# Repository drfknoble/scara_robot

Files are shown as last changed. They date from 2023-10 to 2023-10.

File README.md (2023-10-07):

# Selective Compliance Articulated Robot Arm (SCARA) Project








## Introduction

Welcome to my repository for my Selective Compliance Articulared Robot Arm (SCARA) project.

<!-- <div>
    <img src="./cad/renders/back.png" style="height:240px;">
    <img src="./doc/photos/back.jpg" style="height:240px;">
</div> -->

## Motivation

I started this project because commercial SCARA robots are very expensive and there any low-cost options for me to use in my teaching or research.

## Aims

The aims of this project included:
- Developing a low-cost, SCARA robot that can be used to teach students about mechatronics and robotics.

## Objectives

The objectives of this project included:
- Creating accessible Computer Aided Design (CAD) files.
- Creating accessible Electronics Design Automation (EDA) files.
- Creating accessible source code and software libraries.
- Creating an easy-to-assemble mobile robot that uses a microcontroller, stepper motors, and rotational sensors.

## Repository Structure

The repository is organised as follows:

```console
scara_project/         
    cad/                          
        fabrication/
        parts/
        sub_assemblies/   
    doc/                                   
    eda/
        manipulator_pcb/        
    src/
        esp32_program/
        my_bringup/
        my_scara_1_0_movit_config/
        my_scara_support/
```

All CAD files can be found in the `cad/` sub-directory. I used SolidWorks to create the 3D models of the robot's parts, sub-assemblies, and assembly. Files neeeded to fabricate the robot can be found in the `fabrication/` sub-directory.

All EDA files can be found in the `eda/` sub-directory. I used KiCAD to create the PCB for the robot. Files need to fabricate the PCB can be found in the `manipulator_pcb/` sub-directory.

All source code and software libaries are included in the `src/` sub-directory. I used an ESP32 as the robot's microcontroller and programmed it using PlatformIO's Arduino framework. The ESP32's source code can be found in the `esp32_program/` sub-directory. I also developed a ROS 2 package that makes use of ROS 2 Control and Moveit 2. The package's launch file can be found in the `my_bringup/` sub-directory. 

Documentation is included in the `doc/` sub-directory. I've included a Bill of Materaisl (BOM) file, which includes the compenents used.

## Tools Used

I used the following tools in this project:
- SOLIDWORKS.
- KiCAD.
- Microsoft Visual Studio Code and PlatforIO.
- ROS 2.

Get FreeCAD here: https://www.freecadweb.org/.  
Get KiCAD here: https://www.kicad.org/.  
Get Visual Studio Code here: https://code.visualstudio.com/.  
Get PlatforIO from here: https://platformio.org/. 

## Credit

Dr Frazer K. Noble  
http://drfknoble.com

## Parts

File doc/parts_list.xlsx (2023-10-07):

Item | Description | URL
1 | CNC kit | https://www.amazon.com/Professional-arduino-Mechanical-Endstop-DRV8825/dp/B06Y2BSCL7
2 | Encoder | https://www.amazon.com/Diitao-Magnetic-Precision-Induction-Measurement/dp/B0B4NNK14X
3 | 35 mm thrust bearings | https://www.amazon.com/uxcell-Single-Direction-Thrust-Bearings/dp/B07G847G75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
4 | 40 mm thrust bearings | https://www.amazon.com/uxcell-Single-Direction-Thrust-Bearings/dp/B07G829LM8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
5 | 8 mm Radial bearings | https://www.amazon.com/Bearings-Skateboard-Shielded-Miniature-Skateboards/dp/B07R7PR72H
6 | GT2 belt kit | https://www.amazon.com/3Dman-Timing-Closed-Rubber-Printer/dp/B07WP6VJ66
5 | Arduino Uno | https://mecha4makers.co.nz/product/arduino-uno-clone-usb-b/
5 | CNC shield | https://mecha4makers.co.nz/product/cir-cnc-sh-v3-o1/
15 | Motor driver | https://mecha4makers.co.nz/product/a4988-stepstick-style-stepper-driver-red/
15 | Stepper motor | https://mecha4makers.co.nz/product/17hs3401-s5f-20200829-stepper-motor-5mm-shaft-with-flat/
3 | Encoder | https://www.amazon.com/Alinan-Magnetic-Precision-Induction-Measurement/dp/B09QYC916Q
40 | 8 mm bearing | https://mecha4makers.co.nz/product/ball-bearing-plain-id-6mm/ | Note: | Please order "Plain – ID 8mm OD 22mm Width 7mm 608ZZ" type.
5 | GT2 belt | https://mecha4makers.co.nz/product/gt2-6mm-belts/ | Note: | Please order "Open belt, GT2 x 6mm, polyurethane (black), steel cord (per meter) "
20 | GT2 pulley | https://mecha4makers.co.nz/product/gt2-x-6mm-pulleys-5mm-bore/ | Note: | Pulley GT2 x 6mm wide, 20 teeth, 5mm bore

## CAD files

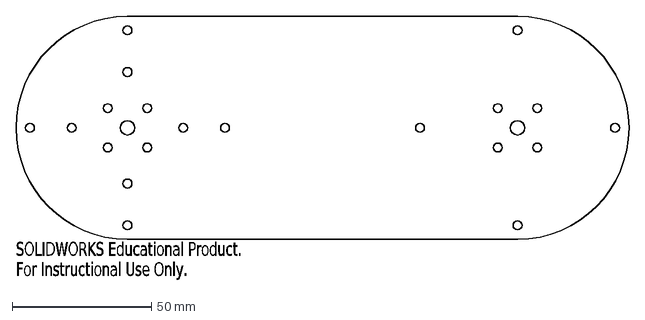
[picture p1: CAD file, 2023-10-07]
cad/fabrication/link_1_bottom.DXF
SOLIDWORKS Educational Product.
For Instructional Use Only.

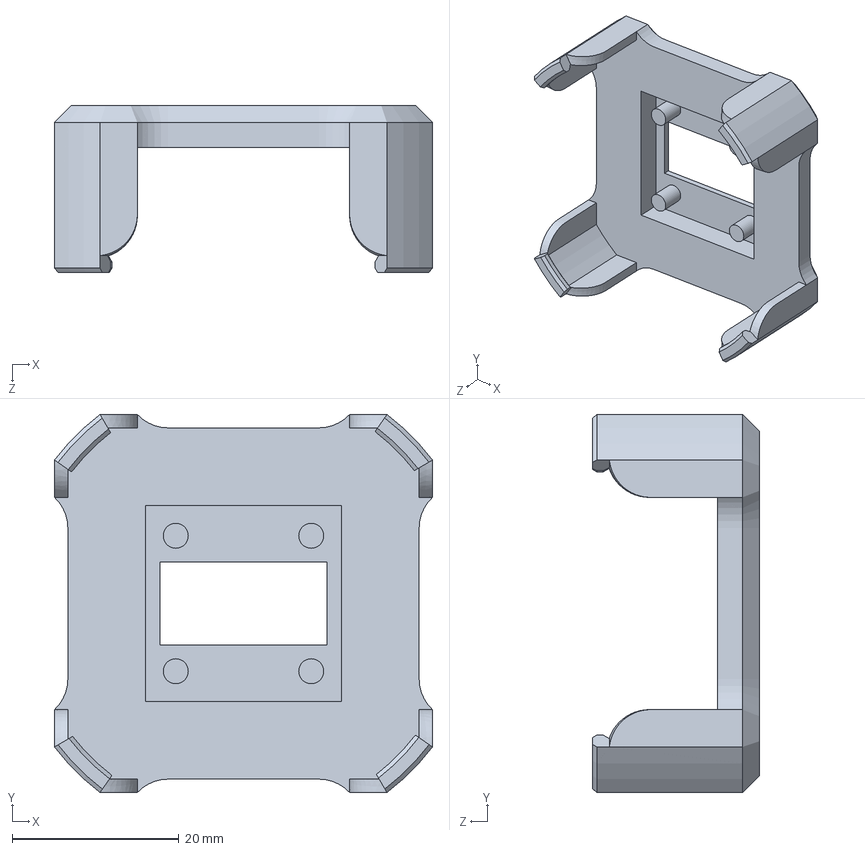
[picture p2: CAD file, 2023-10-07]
cad/parts/encoder_holder.SLDPRT
45.4 x 45.4 x 20.0 mm

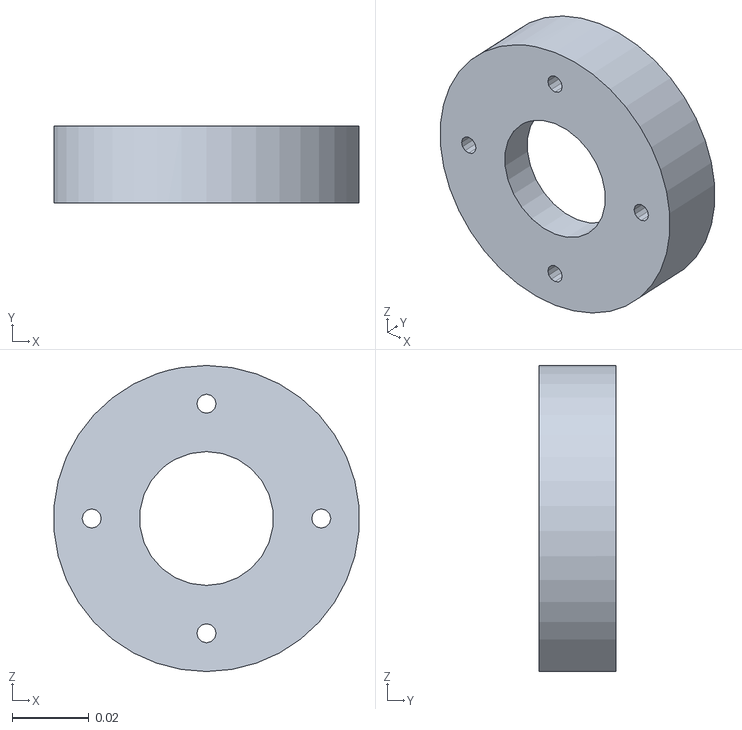
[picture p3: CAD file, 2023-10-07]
src/manipulator/meshes/coupler_1.STL
0.0797 x 0.02 x 0.08

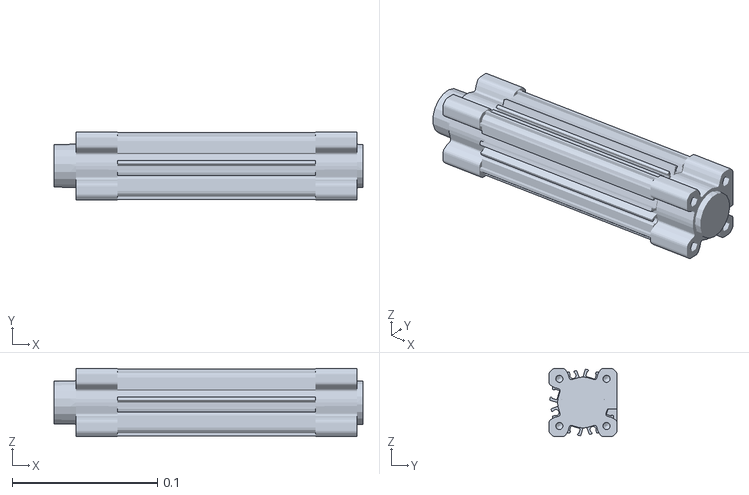
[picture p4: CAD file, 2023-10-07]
src/manipulator_control/meshes/end_effector.STL
0.213 x 0.047 x 0.047

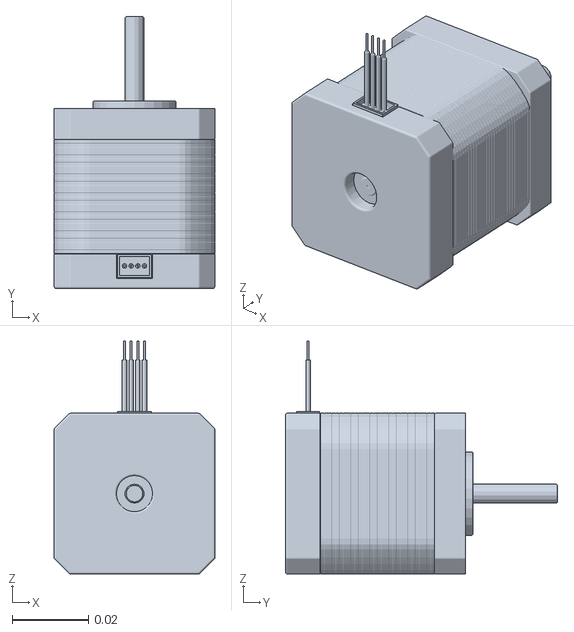
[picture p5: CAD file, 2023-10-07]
src/manipulator_control/meshes/motor_link_1.STL
0.0423 x 0.0716 x 0.0613

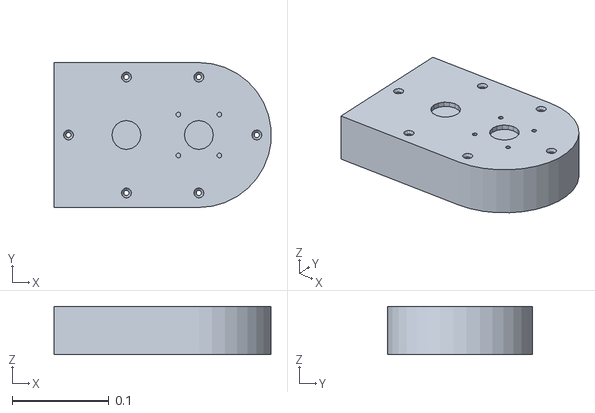
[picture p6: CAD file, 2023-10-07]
src/my_scara_support/meshes/base.STL
0.225 x 0.15 x 0.05

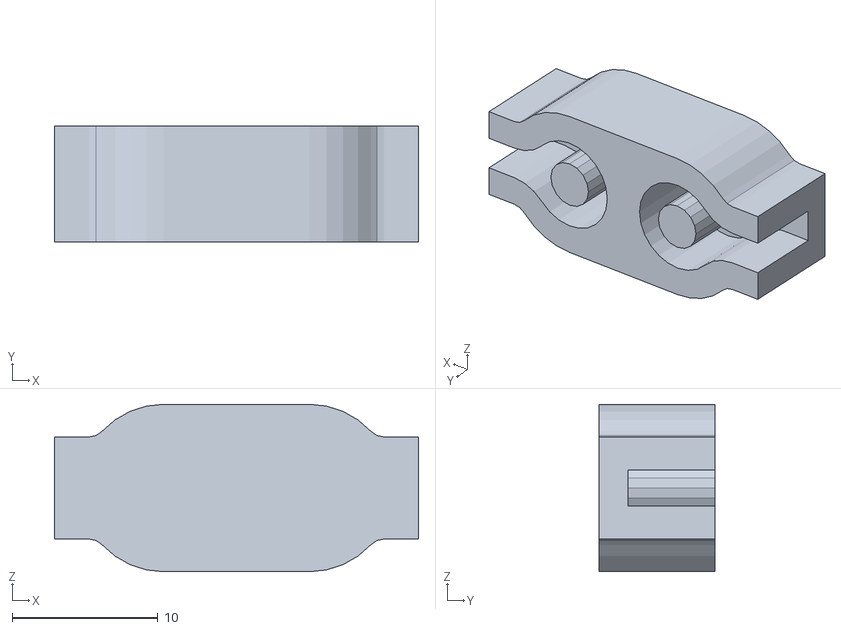
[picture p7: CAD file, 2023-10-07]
cad/fabrication/belt_coupler.STL
25.0 x 8.00 x 11.5

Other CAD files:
src/manipulator/meshes/coupler_2.STL
src/manipulator/meshes/motor_link_2.STL
src/my_scara_support/meshes/coupler_02.STL
src/manipulator_control/meshes/coupler_2.STL
cad/fabrication/link_0_bottom.DXF
cad/fabrication/link_0_top.DXF
cad/fabrication/link_1_top.DXF
cad/fabrication/link_2_top.DXF
cad/fabrication/manipulator - link_0-1 link_0-2-1.STL
cad/fabrication/manipulator - link_0-1 link_0-2.STL
cad/fabrication/manipulator - link_0-1 stepper_motor-1-1.STL
cad/fabrication/manipulator - link_1-1 bearing-1-1.STL
cad/fabrication/manipulator - link_1-1 link_1-1-1.STL
cad/fabrication/manipulator - link_1-1 link_1-1.STL
cad/fabrication/manipulator - link_1-1 stepper_motor-1-1.STL
cad/fabrication/manipulator - link_1-1 stepper_motor-1.STL
cad/fabrication/manipulator - link_2-2 bearing-1-1.STL
cad/fabrication/manipulator - link_2-2 link_2-1-1.STL
src/manipulator/meshes/link_1.STL
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

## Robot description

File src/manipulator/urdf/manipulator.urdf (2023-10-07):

<?xml version="1.0" encoding="utf-8"?>
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
<robot name="manipulator">
  <link name="base_link">
    <inertial>
      <origin xyz="0.029207 -2.8317E-17 0.024645" rpy="0 0 0" />
      <mass value="1.253" />
      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
    </inertial>
    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
  </link>
  <link name="coupler_1">
    <inertial>
      <origin xyz="-6.93889390390723E-17 0.0072813688212928 -1.52926106285397E-16" rpy="0 0 0" />
      <mass value="0.139427808957131" />
      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
    </inertial>
    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
  </link>
  <joint name="joint_1" type="continuous">
    <origin xyz="0.075 0 0.05" rpy="1.5708 0 0" />
    <parent link="base_link" />
    <child link="coupler_1" />
    <axis xyz="0 1 0" />
    <limit lower="-1.5708" upper="1.5708" effort="0" velocity="0" />
  </joint>
  <link name="link_1">
    <inertial>
      <origin xyz="0.07 0.0250821742955448 1.19366003801782E-17" rpy="0 0 0" />
      <mass value="0.721333334319362" />
      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
    </inertial>
    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
  </link>
  <joint name="weld_1" type="fixed">
    <origin xyz="0 0.02 0" rpy="0 0 0" />
    <parent link="coupler_1" />
    <child link="link_1" />
    <axis xyz="0 0 0" />
  </joint>
  <link name="coupler_2">
    <inertial>
      <origin xyz="-2.77555756156289E-17 0.00728136882129281 -1.53599210807692E-16" rpy="0 0 0" />
      <mass value="0.139427808957131" />
      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
    </inertial>
    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
  </link>
  <joint name="joint_2" type="continuous">
    <origin xyz="0.14 0.05 0" rpy="0 0 0" />
    <parent link="link_1" />
    <child link="coupler_2" />
    <axis xyz="0 1 0" />
    <limit lower="-1.5708" upper="1.5708" effort="0" velocity="0" />
  </joint>
  <link name="link_2">
    <inertial>
      <origin xyz="0.07 0.0150687991093598 5.45898405902557E-18" rpy="0 0 0" />
      <mass value="0.553340131043985" />
      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
    </inertial>
    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
  </link>
  <joint name="weld_2" type="fixed">
    <origin xyz="0 0.02 0" rpy="0 0 0" />
    <parent link="coupler_2" />
    <child link="link_2" />
    <axis xyz="0 0 0" />
  </joint>
  <link name="end_effector">
    <inertial>
      <origin xyz="0.100349198973376 0.000353822159549988 6.33217529944508E-12" rpy="0 0 0" />
      <mass value="0.229959232623262" />
      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
    </inertial>
    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
  </link>
  <joint name="weld_3" type="fixed">
    <origin xyz="0.14 0.03 0" rpy="0 0 1.57079632679489" />
    <parent link="link_2" />
    <child link="end_effector" />
    <axis xyz="0 0 0" />
  </joint>
  <link name="motor_link_2">
    <inertial>
      <origin xyz="-1.93846480835157E-17 0.024090333234571 1.45866755534296E-05" rpy="0 0 0" />
      <mass value="0.0817024345002187" />
      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
    </inertial>
    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
  </link>
  <joint name="motor_weld_2" type="fixed">
    <origin xyz="0 0.0974 0" rpy="3.14159265358979 1.5707963267949 0" />
    <parent link="link_1" />
    <child link="motor_link_2" />
    <axis xyz="0 0 0" />
  </joint>
  <link name="motor_link_1">
    <inertial>
      <origin xyz="0 0 0" rpy="0 0 0" />
      <mass value="0" />
      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
    </inertial>
    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
  </link>
  <joint name="motor_weld_1" type="fixed">
    <origin xyz="0 0 0.0974" rpy="-1.5707963267949 0 1.5707963267949" />
    <parent link="base_link" />
    <child link="motor_link_1" />
    <axis xyz="0 0 0" />
  </joint>
</robot>

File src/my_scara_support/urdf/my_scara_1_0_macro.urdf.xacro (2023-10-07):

<?xml version="1.0"?>
<robot xmlns:xacro="http://www.ros.org/wiki/xacro">
    <xacro:macro name="my_scara_1_0_macro">
        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
        <link name="base">
            <inertial>
            <origin xyz="0.029207 -2.9211E-17 0.024645" rpy="0 0 0" />
            <mass value="1.253" />
            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
            </inertial>
            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
        </link>
        <link name="coupler_01">
            <inertial>
            <origin xyz="-6.93889390390723E-17 0.0072813688212928 -1.52921972221633E-16" rpy="0 0 0" />
            <mass value="0.139427808957131" />
            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
            </inertial>
            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
        </link>
        <link name="link_01">
            <inertial>
            <origin xyz="0.07 0.0250821742955448 1.18862872341622E-17" rpy="0 0 0" />
            <mass value="0.721333334319361" />
            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
            </inertial>
            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
        </link>
        <link name="coupler_02">
            <inertial>
            <origin xyz="-2.77555756156289E-17 0.00728136882129281 -1.53599396082019E-16" rpy="0 0 0" />
            <mass value="0.139427808957131" />
            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
            </inertial>
            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
        </link>
        <link name="link_02">
            <inertial>
            <origin xyz="0.07 0.0150687991093598 5.47005078454743E-18" rpy="0 0 0" />
            <mass value="0.553340131043985" />
            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
            </inertial>
            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
        </link>
        <link name="end_effector">
            <inertial>
            <origin xyz="0.100349198973376 0.000353822159549988 6.33217478009659E-12" rpy="0 0 0" />
            <mass value="0.229959232623262" />
            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
            </inertial>
            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
        </link>
        <link name="motor_02">
            <inertial>
            <origin xyz="-1.93256233677813E-17 0.0240903332345709 1.45866755534296E-05" rpy="0 0 0" />
            <mass value="0.0817024345002187" />
            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
            </inertial>
            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
        </link>
        <link name="motor_01">
            <inertial>
            <origin xyz="0 0 0" rpy="0 0 0" />
            <mass value="0" />
            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
            </inertial>
            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
        </link>
        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
        <joint name="joint_1" type="revolute">
            <origin xyz="0.075 0 0.05" rpy="1.5708 0 0" />
            <parent link="base" />
            <child link="coupler_01" />
            <axis xyz="0 1 0" />
            <limit lower="-1.5708" upper="+1.5708" effort="0" velocity="0" />
        </joint>
        <joint name="joint_2" type="revolute">
            <origin xyz="0.14 0.05 0" rpy="0 0 0" />
            <parent link="link_01" />
            <child link="coupler_02" />
            <axis xyz="0 1 0" />
            <limit lower="-1.5708" upper="+1.5708" effort="0" velocity="0" />
        </joint>
        <joint name="weld_motor_01" type="fixed">
            <origin xyz="0 0 0.0974" rpy="-1.5708 0 1.5708" />
            <parent link="base" />
            <child link="motor_01" />
            <axis xyz="0 0 0" />
        </joint>
        <joint name="weld_motor_02" type="fixed">
            <origin xyz="0 0.0974 0" rpy="3.14159 1.5708 0" />
            <parent link="link_01" />
            <child link="motor_02" />
            <axis xyz="0 0 0" />
        </joint>
        <joint name="weld_01" type="fixed">
            <origin xyz="0 0.02 0" rpy="0 0 0" />
            <parent link="coupler_01" />
            <child link="link_01" />
            <axis xyz="0 0 0" />
        </joint>
        <joint name="weld_02" type="fixed">
            <origin xyz="0 0.02 0" rpy="0 0 0" />
            <parent link="coupler_02" />
            <child link="link_02" />
            <axis xyz="0 0 0" />
        </joint>
        <joint name="weld_03" type="fixed">
            <origin xyz="0.14 0.03 0" rpy="0 0 1.5708" />
            <parent link="link_02" />
            <child link="end_effector" />
            <axis xyz="0 0 0" />
        </joint>
        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
    </xacro:macro>
</robot>

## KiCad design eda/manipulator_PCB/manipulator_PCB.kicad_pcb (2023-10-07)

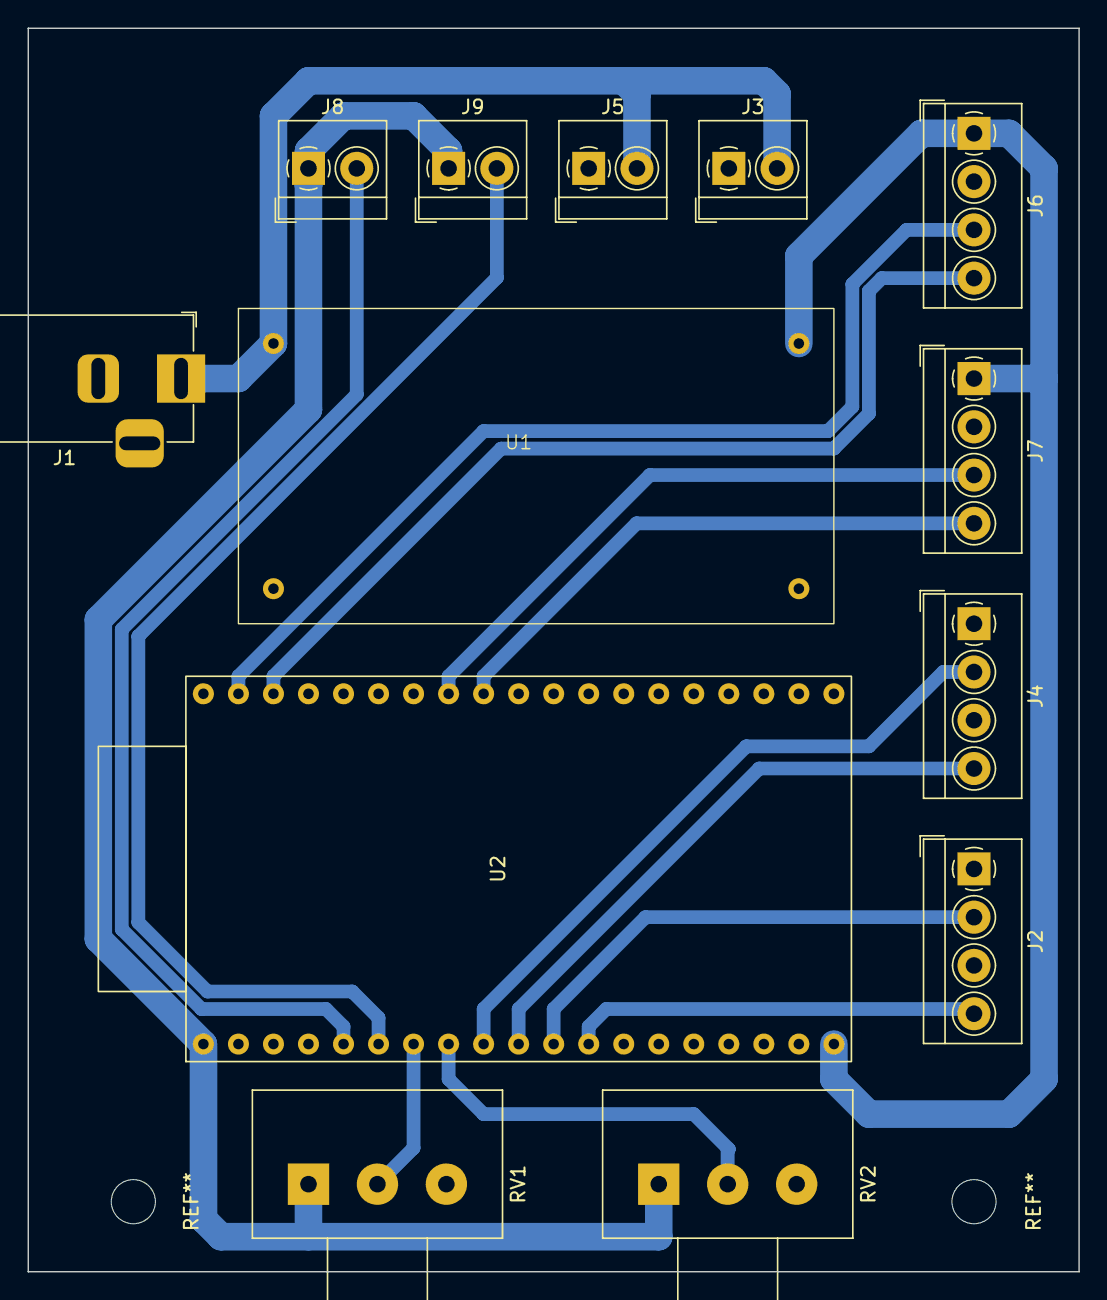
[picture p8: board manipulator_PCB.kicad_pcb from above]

Board: 2 copper layers, 76.2 x 90.2 mm, 13 parts (0 on the bottom side), 16 nets.

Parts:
J1: Barrel_Jack_Switch_Pin3Ring; BarrelJack_Horizontal
J2, J4, J6, J7: Screw_Terminal_01x04; TerminalBlock_4Ucon_1x04_P3.50mm_Horizontal
J3, J5, J8, J9: Screw_Terminal_01x02; TerminalBlock_4Ucon_1x02_P3.50mm_Horizontal
RV1, RV2: 10K; Potentiometer_Alps_RK163_Single_Horizontal
U1: DC-DC_Converter
U2: ESP32-DevKitC

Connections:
+3V3: J8.1, J9.1, RV1.1, RV2.1, U2.1 (3V3)
+5V: J6.1, J7.1, U1.4 (VOUT+), U2.19 (5V0)
+12V: J1.1, J3.2, J5.2, U1.1 (VIN+)
DIR1: J2.2, U2.11 (27)
DIR2: J4.2, U2.9 (25)
GND: J1.2, J1.3, J2.1, J2.3, J3.1, J4.1, J4.3, J5.1, J6.2, J7.2, RV1.3, RV2.3, U1.2 (VIN-), U1.3 (VOUT-), U2.14 (GND), U2.32 (GND), U2.38 (GND)
unnamed: RV1.2, U2.7 (32)
unnamed: RV2.2, U2.8 (33)
SCL1: J6.4, U2.36 (22)
SCL2: J7.4, U2.30 (18)
SDA1: J6.3, U2.37 (23)
SDA2: J7.3, U2.31 (19)
STEP1: J2.4, U2.12 (14)
STEP2: J4.4, U2.10 (26)
lim1: J8.2, U2.5 (34)
lim2: J9.2, U2.6 (35)

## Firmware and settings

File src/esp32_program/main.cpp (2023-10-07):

#include <Arduino.h>
#include <Wire.h>

// Configure I2C for joint 1 and 2's encoders.
TwoWire encoder1{ 0 }; // = TwoWire(0);
TwoWire encoder2{ 1 }; // = TwoWire(1);

/***
 * @brief. Defines GPIO pins and sets I/O state. 
 * 
 * @param. void.
 * @return void.
 */
void setup()
{
    encoder1.begin(GPIO_NUM_23, GPIO_NUM_22);
    encoder2.begin(GPIO_NUM_19, GPIO_NUM_18);
    
    // configure serial port.
    Serial.begin(115200);

    // Configure LEDs
    pinMode(GPIO_NUM_16, OUTPUT);
    digitalWrite(GPIO_NUM_16, HIGH);
    pinMode(GPIO_NUM_17, OUTPUT);
    digitalWrite(GPIO_NUM_17, HIGH);

    // Configure stepper 1
    // Direction pin 1 (dir1)
    pinMode(GPIO_NUM_27, OUTPUT);
    digitalWrite(GPIO_NUM_27, LOW);
    // Step pin 1 (step1)
    pinMode(GPIO_NUM_14, OUTPUT);
    digitalWrite(GPIO_NUM_14, LOW);

    // Configure stepper 2
    // Direction pin 2 (dir2)
    pinMode(GPIO_NUM_25, OUTPUT);
    digitalWrite(GPIO_NUM_25, LOW);
    // Step pin 2 (step2)
    pinMode(GPIO_NUM_26, OUTPUT);
    digitalWrite(GPIO_NUM_14, LOW);

    // configure analog inputs
    pinMode(GPIO_NUM_32, INPUT);
    pinMode(GPIO_NUM_33, INPUT);

}

/***
 * @brief. Reads and writes to GPIO pins.
 * 
 * @param. void.
 * @return. void.
*/
void loop()
{
    // Get data from analog inputs
    int analogInput1 = analogRead(GPIO_NUM_33);
    int analogInput2 = analogRead(GPIO_NUM_32);

    // Map analog value to joint limits
    float desiredAngle1 = (200 + 2700 * (float)analogInput1 / 4096);
    float desiredAngle2 = (1600 + 2200 * (float)analogInput2 / 4096);

    // Get angle from encoder 1
    encoder1.beginTransmission(0x36);
    encoder1.write(0x0E);
    encoder1.endTransmission();

    encoder1.requestFrom(0x36, 2);
    int data1 = encoder1.read();
    data1 <<= 8;
    data1 += encoder1.read();
    float angle1 = (float)data1;

    // Get angle from encoder 2
    encoder2.beginTransmission(0x36);
    encoder2.write(0x0E);
    encoder2.endTransmission();

    encoder2.requestFrom(0x36, 2);
    int data2 = encoder2.read();
    data2 <<= 8;
    data2 += encoder2.read();
    float angle2 = (float)data2;

    // Compute difference between set point and measured angle
    float error1 = desiredAngle1 - angle1;
    float error2 = desiredAngle2 - angle2;

    // A simple PID algorithm for joints 1 and 2
    if (error1 > +1.8 / 0.09) 
    {
        // angle is less than desired angle, move clockwise
        digitalWrite(GPIO_NUM_25, HIGH);
        digitalWrite(GPIO_NUM_26, HIGH);
        delay(10);
        digitalWrite(GPIO_NUM_26, LOW);
        delay(10);
        // angle1 = angle1 + 1.8;

    }
    else if (error1 < -1.8 / 0.09)
    {
        // angle is greater than desired angle, move anticlockwise
        digitalWrite(GPIO_NUM_25, LOW);
        digitalWrite(GPIO_NUM_26, HIGH);
        delay(10);
        digitalWrite(GPIO_NUM_26, LOW);
        delay(10);
        // angle1 = angle1 - 1.8;
    }

    if (error2 > +1.8 / 0.09) 
    {
        // angle is less than desired angle, move clockwise
        digitalWrite(GPIO_NUM_27, HIGH);
        digitalWrite(GPIO_NUM_14, HIGH);
        delay(10);
        digitalWrite(GPIO_NUM_14, LOW);
        delay(10);
        // Serial.println(angle1);
        // angle2 = angle2 + 1.8;

    }
    else if (error2 < -1.8 / 0.09)
    {
        // angle is greater than desired angle, move anticlockwise
        digitalWrite(GPIO_NUM_27, LOW);
        digitalWrite(GPIO_NUM_14, HIGH);
        delay(10);
        digitalWrite(GPIO_NUM_14, LOW);
        delay(10);
        // Serial.println(angle1);
        // angle2 = angle2 - 1.8;
    }


    char buf[100];
    sprintf(buf, "%f:%f:%f, %f:%f:%f", desiredAngle1, angle1, error1, desiredAngle2, angle2, error2);
    Serial.println(buf);

}

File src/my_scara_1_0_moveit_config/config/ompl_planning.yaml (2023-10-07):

planning_plugin: ompl_interface/OMPLPlanner
request_adapters: >-
  default_planner_request_adapters/AddTimeParameterization
  default_planner_request_adapters/ResolveConstraintFrames
  default_planner_request_adapters/FixWorkspaceBounds
  default_planner_request_adapters/FixStartStateBounds
  default_planner_request_adapters/FixStartStateCollision
  default_planner_request_adapters/FixStartStatePathConstraints
start_state_max_bounds_error: 0.1
planner_configs:
  SBLkConfigDefault:
    type: geometric::SBL
    range: 0.0  # Max motion added to tree. ==> maxDistance_ default: 0.0, if 0.0, set on setup()
  ESTkConfigDefault:
    type: geometric::EST
    range: 0.0  # Max motion added to tree. ==> maxDistance_ default: 0.0, if 0.0 setup()
    goal_bias: 0.05  # When close to goal select goal, with this probability. default: 0.05
  LBKPIECEkConfigDefault:
    type: geometric::LBKPIECE
    range: 0.0  # Max motion added to tree. ==> maxDistance_ default: 0.0, if 0.0, set on setup()
    border_fraction: 0.9  # Fraction of time focused on boarder default: 0.9
    min_valid_path_fraction: 0.5  # Accept partially valid moves above fraction. default: 0.5
  BKPIECEkConfigDefault:
    type: geometric::BKPIECE
    range: 0.0  # Max motion added to tree. ==> maxDistance_ default: 0.0, if 0.0, set on setup()
    border_fraction: 0.9  # Fraction of time focused on boarder default: 0.9
    failed_expansion_score_factor: 0.5  # When extending motion fails, scale score by factor. default: 0.5
    min_valid_path_fraction: 0.5  # Accept partially valid moves above fraction. default: 0.5
  KPIECEkConfigDefault:
    type: geometric::KPIECE
    range: 0.0  # Max motion added to tree. ==> maxDistance_ default: 0.0, if 0.0, set on setup()
    goal_bias: 0.05  # When close to goal select goal, with this probability. default: 0.05
    border_fraction: 0.9  # Fraction of time focused on boarder default: 0.9 (0.0,1.]
    failed_expansion_score_factor: 0.5  # When extending motion fails, scale score by factor. default: 0.5
    min_valid_path_fraction: 0.5  # Accept partially valid moves above fraction. default: 0.5
  RRTkConfigDefault:
    type: geometric::RRT
    range: 0.0  # Max motion added to tree. ==> maxDistance_ default: 0.0, if 0.0, set on setup()
    goal_bias: 0.05  # When close to goal select goal, with this probability? default: 0.05
  RRTConnectkConfigDefault:
    type: geometric::RRTConnect
    range: 0.0  # Max motion added to tree. ==> maxDistance_ default: 0.0, if 0.0, set on setup()
  RRTstarkConfigDefault:
    type: geometric::RRTstar
    range: 0.0  # Max motion added to tree. ==> maxDistance_ default: 0.0, if 0.0, set on setup()
    goal_bias: 0.05  # When close to goal select goal, with this probability? default: 0.05
    delay_collision_checking: 1  # Stop collision checking as soon as C-free parent found. default 1
  TRRTkConfigDefault:
    type: geometric::TRRT
    range: 0.0  # Max motion added to tree. ==> maxDistance_ default: 0.0, if 0.0, set on setup()
    goal_bias: 0.05  # When close to goal select goal, with this probability? default: 0.05
    max_states_failed: 10  # when to start increasing temp. default: 10
    temp_change_factor: 2.0  # how much to increase or decrease temp. default: 2.0
    min_temperature: 10e-10  # lower limit of temp change. default: 10e-10
    init_temperature: 10e-6  # initial temperature. default: 10e-6
    frountier_threshold: 0.0  # dist new state to nearest neighbor to disqualify as frontier. default: 0.0 set in setup()
    frountierNodeRatio: 0.1  # 1/10, or 1 nonfrontier for every 10 frontier. default: 0.1
    k_constant: 0.0  # value used to normalize expresssion. default: 0.0 set in setup()
  PRMkConfigDefault:
    type: geometric::PRM
    max_nearest_neighbors: 10  # use k nearest neighbors. default: 10
  PRMstarkConfigDefault:
    type: geometric::PRMstar
  FMTkConfigDefault:
    type: geometric::FMT
    num_samples: 1000  # number of states that the planner should sample. default: 1000
    radius_multiplier: 1.1  # multiplier used for the nearest neighbors search radius. default: 1.1
    nearest_k: 1  # use Knearest strategy. default: 1
    cache_cc: 1  # use collision checking cache. default: 1
    heuristics: 0  # activate cost to go heuristics. default: 0
    extended_fmt: 1  # activate the extended FMT*: adding new samples if planner does not finish successfully. default: 1
  BFMTkConfigDefault:
    type: geometric::BFMT
    num_samples: 1000  # number of states that the planner should sample. default: 1000
    radius_multiplier: 1.0  # multiplier used for the nearest neighbors search radius. default: 1.0
    nearest_k: 1  # use the Knearest strategy. default: 1
    balanced: 0  # exploration strategy: balanced true expands one tree every iteration. False will select the tree with lowest maximum cost to go. default: 1
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

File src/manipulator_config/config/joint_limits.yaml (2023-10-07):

# joint_limits.yaml allows the dynamics properties specified in the URDF to be overwritten or augmented as needed

# For beginners, we downscale velocity and acceleration limits.
# You can always specify higher scaling factors (<= 1.0) in your motion requests.  # Increase the values below to 1.0 to always move at maximum speed.
default_velocity_scaling_factor: 0.1
default_acceleration_scaling_factor: 0.1

# Specific joint properties can be changed with the keys [max_position, min_position, max_velocity, max_acceleration]
# Joint limits can be turned off with [has_velocity_limits, has_acceleration_limits]
joint_limits:
  joint_1:
    has_velocity_limits: false
    max_velocity: 0
    has_acceleration_limits: false
    max_acceleration: 0
  joint_2:
    has_velocity_limits: false
    max_velocity: 0
    has_acceleration_limits: false
    max_acceleration: 0
